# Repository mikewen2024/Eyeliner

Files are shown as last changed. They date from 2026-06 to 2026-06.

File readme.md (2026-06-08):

# Eyeliner — Melty-Brain Combat Robot

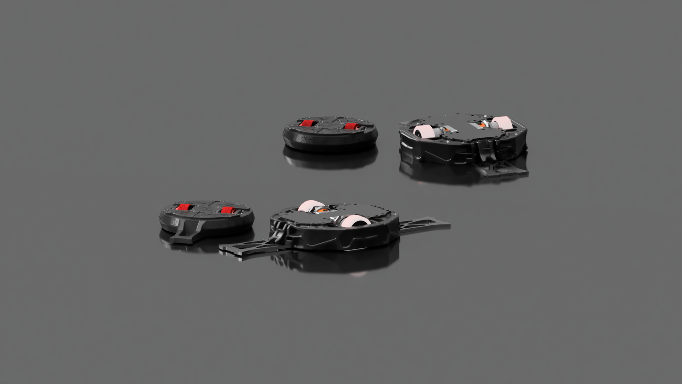
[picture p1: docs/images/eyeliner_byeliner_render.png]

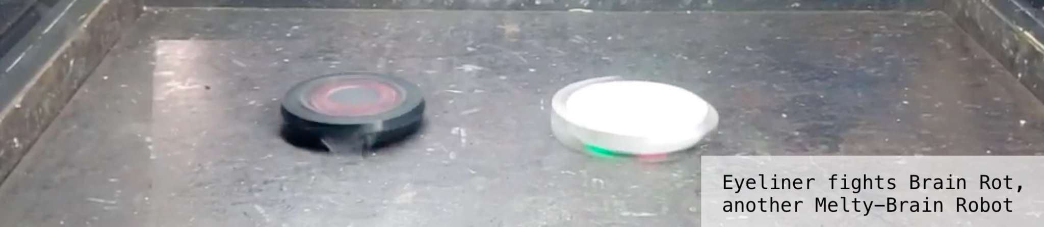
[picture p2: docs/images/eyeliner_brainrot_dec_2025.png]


A 1lb (antweight) melty-brain combat robot. A melty-brain spins the entire chassis at 1,000–2,000 RPM while pulsing drive motors ~100 times/second to achieve controlled translational movement — maximum hitting power, and one of the hardest archetypes to execute correctly.

**Key system requirements:** MHz-range onboard MCU, high-range accelerometer (~400g) for RPM/heading, per-motor drive current of ~30A (≈500W), and all electronics surviving constant 200–300g with peak impact accelerations orders of magnitude higher.

To read more about the development of the project and past versions, check out my personal technical blog [here](https://future-wool-0d5.notion.site/Eyeliner-Melty-brain-Combat-Robot-2ede4d628bf380b29920f43a3518d5c0) :)

---

## Current Iteration

**Hardware:** XIAO ESP32-S3 PLUS MCU, LSM6DSV320X IMU, Repeat Robotics BEC, ELRS nano receiver, dual 35A ESCs, ws2812b LED strip, Standalone ADXL-375 Accelerometer

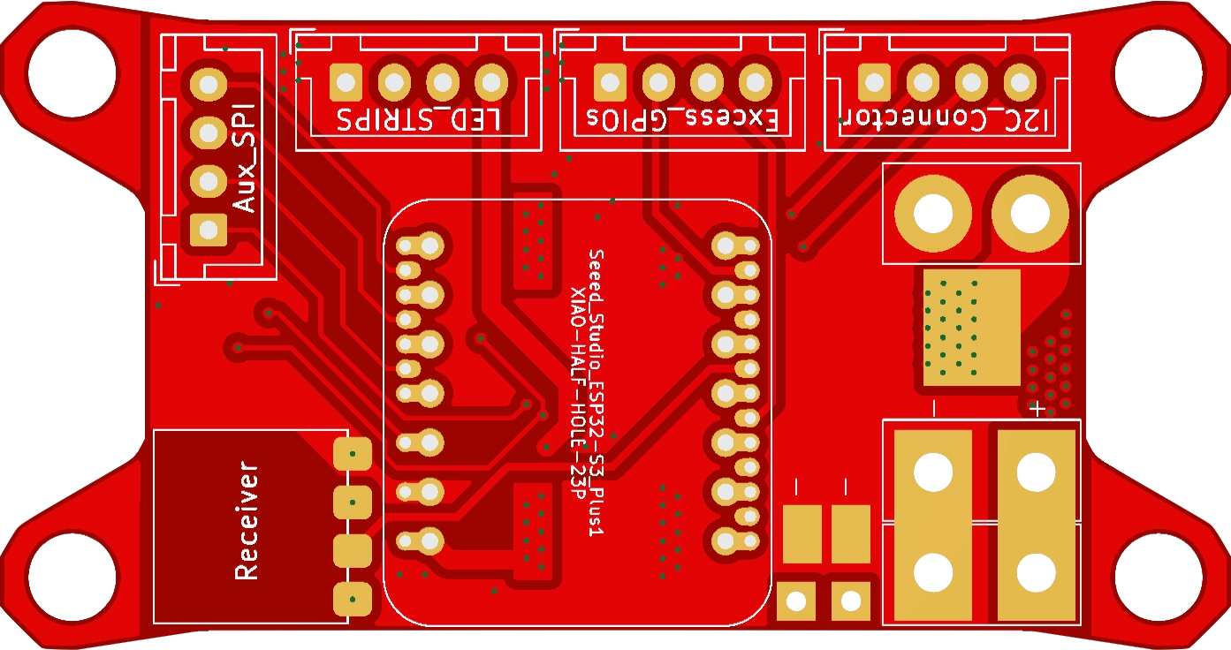
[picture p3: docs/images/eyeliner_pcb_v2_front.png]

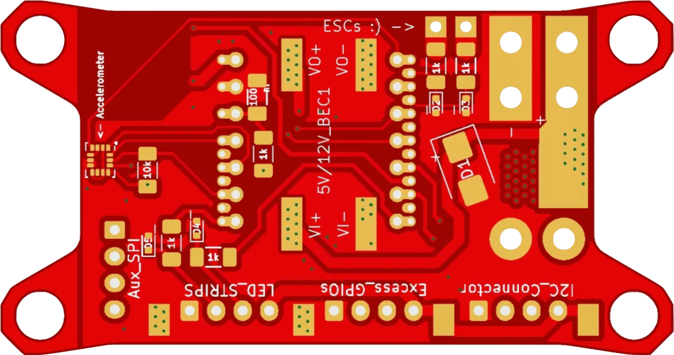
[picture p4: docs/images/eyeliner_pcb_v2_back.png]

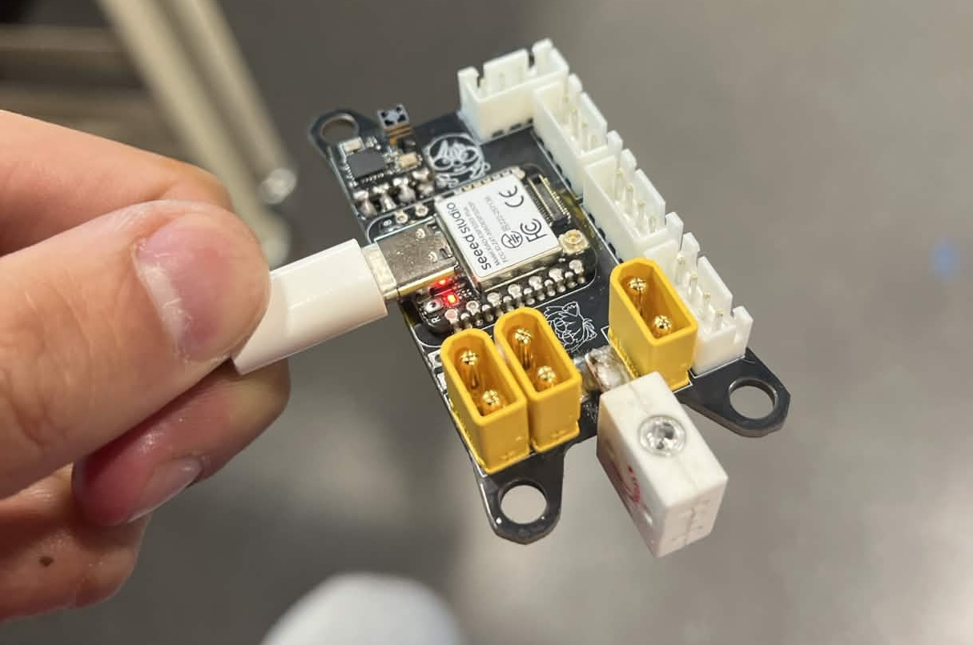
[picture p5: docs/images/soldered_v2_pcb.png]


**Key Features:**

- Extensive consideration for signal integrity, decoupling and bulk capacitance, and transients protection on all vulnerable MCU GPIO ports
- Made to run on 4s-6s LiHV with minimal changes (TVS diode change), interface with a range of possible sensors, and run interchangeably with antweight and beetleweight electronics
- Interchangeable high-kv 2207 "pacer" motors (outright top-range hitting power) and low-kv 2822 motors (faster spin-up with less current draw)
- LSM6DSV320X IMU with high and low range readout registers, built-in impact detection and interrupt capability, SPI interface 
- Custom UART interface for ELRS receiver to improve signal stability and expand channel bandwidth to 16 channels 
- LED strips for better heading and state indication
- Spare set of SPI connections for standalone ADXL375 or other sensors
- Shock isolated mounting with bracing for connectors
- Judicious ground plane placement for good return paths and receiver signal integrity, high-speed trace routing to reduce cross-talk and RC-loss, balancing current surge protection and voltage surge protection with TVS Diodes
- Up to 2500W burst capacity on HV side via solder busses, structural stability via extensive via stitching
- Spare GPIO connections for thermistors, IR sensors, etc...
- DSHOT600 and DSHOT1200 for high rate and accurate motor torque control at speed, built-in twisted-pairs for signal lines with GND return paths as close as possible to ESC grounds

**Upcoming Changes:** 

- Dual H3LIS331DL accelerometers (rotational speed without knowing center of rotation), easier-to-solder footprint
- More robust LDO system for 5V side
- Precharge circuit for higher-voltage inputs
- Two-way DSHOT for traction control
- Easily-removable high-speed connectors for ESCs
- Switch to STM32 for higher clock speeds, ESP32 for telemetry and LED control only
- Custom sensored ESCs
- Custom BMS

---

### Byeliner — Beetleweight Upscale V0 *(March 2026 – Present)*
**Class:** 3lb (beetleweight)
**Hardware Changes:** Oversize 790 kV 3548 motors, dual 80A 8s-capable VORTEX F65 ESCs, dual 4s LiHV batteries

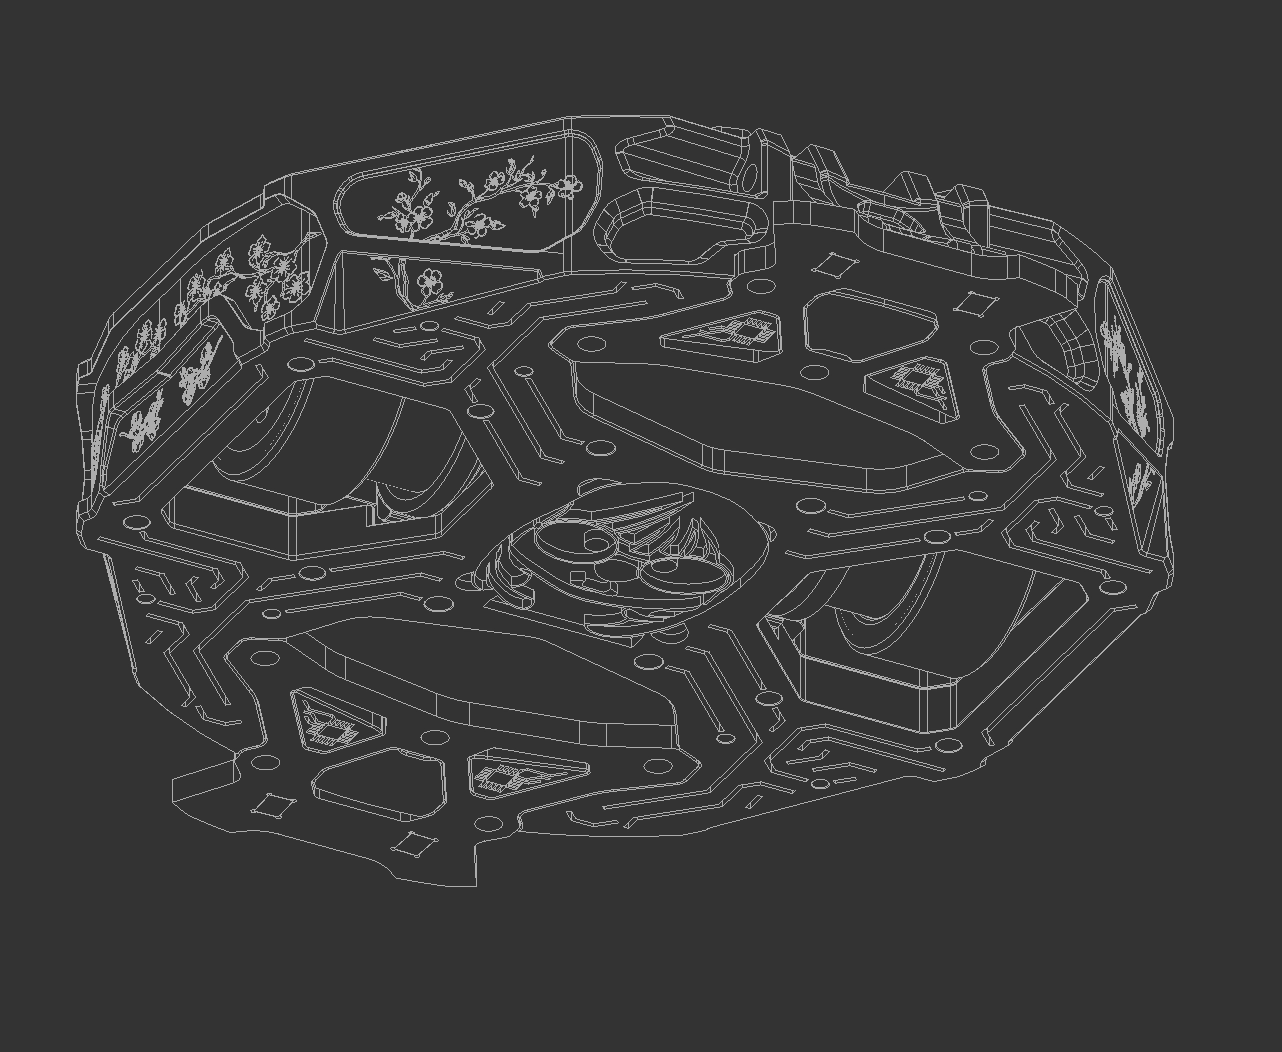
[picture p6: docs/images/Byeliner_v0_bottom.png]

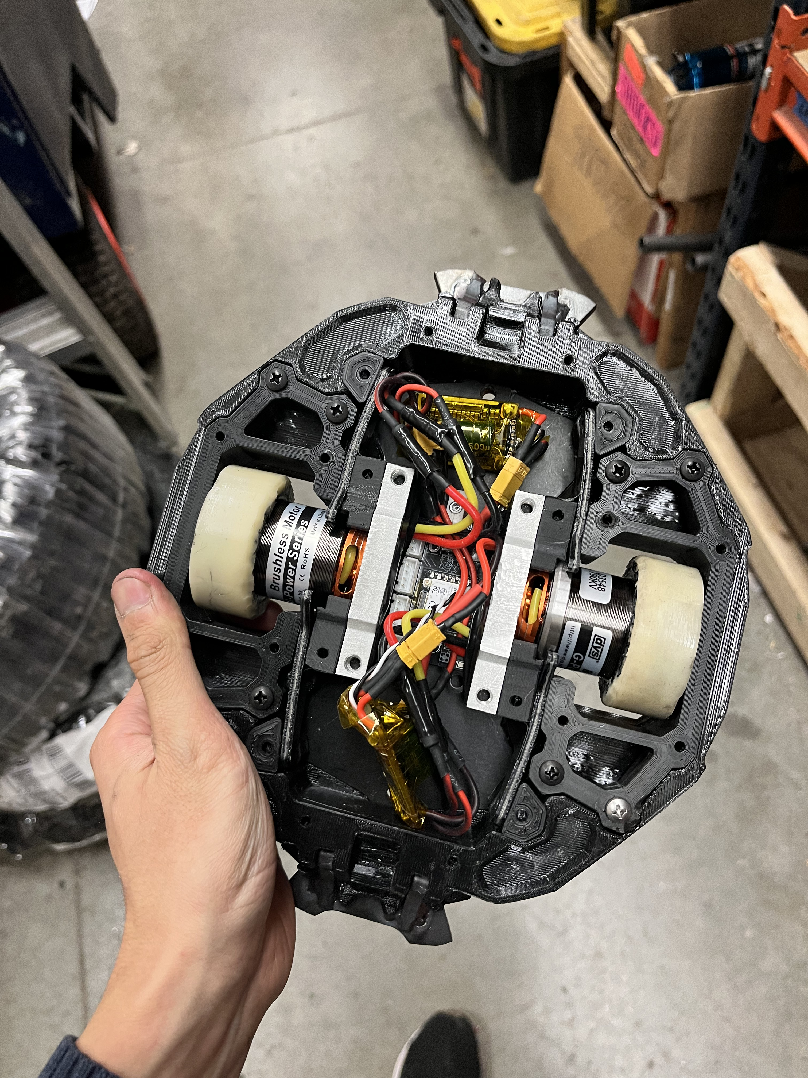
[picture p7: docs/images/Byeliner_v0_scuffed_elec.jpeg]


A 3lb version ("Byeliner") built for **Robobrawl**, early April 2026. The chassis is a rigid CURV and aluminum skeleton wrapped in TPU. On the code side, we are also moving towards platformIO for more organized operation.

---

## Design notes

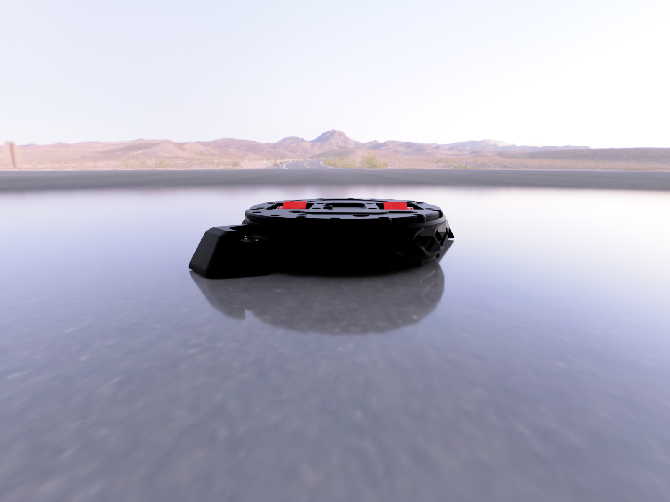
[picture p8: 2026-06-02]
docs/images/eyeliner_summer_2025_render.png

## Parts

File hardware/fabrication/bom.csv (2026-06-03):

Designator | Footprint | Quantity | Value | LCSC Part #
+, XT-30_VERT1, XT-30_VERT3 | XT-30_VERT | 3 | ~
100 | 1206 | 1 | 100 nF
10K, 1K | 1206 | 2 | 10k
1K_5, 1K_4, 1K_3, 1K_2 | 1206 | 4 | 1k
5V/12V_BEC1 | BEC_5V_12V | 1 | ~
<- ACCELEROMETER | LGA-14_3x2.5mm_P0.5mm_LayoutBorder3x4y | 1 | LSM6DSV320XTR
D1 | D_SMB | 1 | D_TVS
D2, D3 | D_SOD-523 | 2 | D_TVS
D4 | D_SOD-523 | 1 | D_LED_1
D5 | D_SOD-523 | 1 | D_LED_2
ESC1, ESC2 | ESC-PWM-Connection | 2 | ~
FINGERTECH_SWITCH1 | Fingertech_Switch | 1 | ~
J1 | JST_XH_B4B-XH-A_1x04_P2.50mm_Vertical | 1 | LED_STRIPS
J2 | JST_XH_B4B-XH-A_1x04_P2.50mm_Vertical | 1 | Aux_SPI
J3 | JST_XH_B4B-XH-A_1x04_P2.50mm_Vertical | 1 | I2C_Connector
J4 | JST_XH_B4B-XH-A_1x04_P2.50mm_Vertical | 1 | Excess_GPIOs
RECEIVER | BetaFPV ELRS Lite | 1 | ~
SEEED_STUDIO_ESP32-S3_PLUS1 | MOUDLE23P-SMD-2.54-21X17.8MM.kicad_mod.kicad_sym | 1 | XIAO-HALF-HOLE-23P
U1, U2, U3, U4, U5, U6 | Generic_SMD_THT | 6 | ~

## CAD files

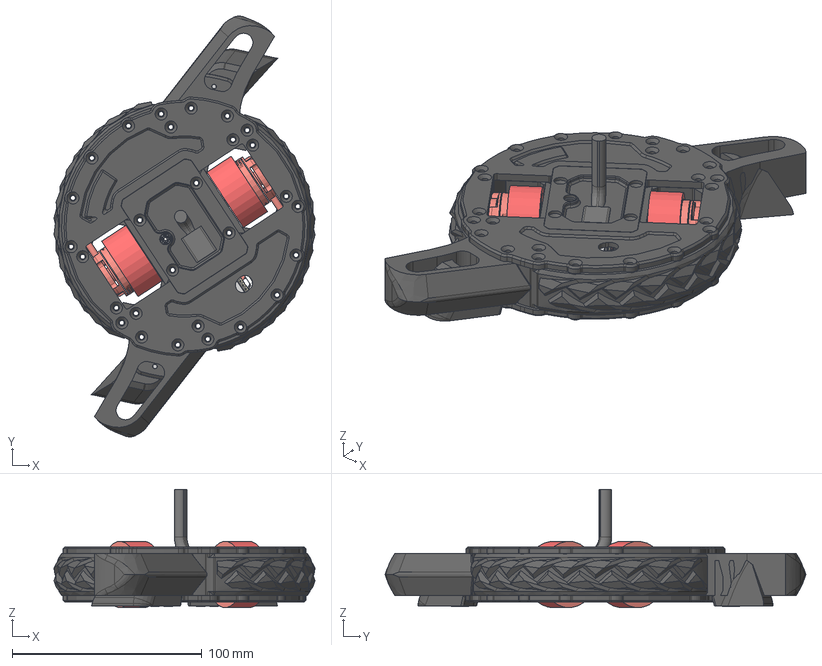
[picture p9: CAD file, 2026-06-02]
mechanical/PLANT_standalone_teeth/Main CAD.step
137.7 x 222.0 x 62.3 mm
Standard Weapon Teeth
BOSS-EXTRUDE14_8_
BOSS-EXTRUDE7_4_
BOSS-EXTRUDE7_3_
BOSS-EXTRUDE14_4_
BOSS-EXTRUDE14_2_
BOSS-EXTRUDE14_11_
BOSS-EXTRUDE7_7_
BOSS-EXTRUDE14_9_
BOSS-EXTRUDE14_3_
BOSS-EXTRUDE14_7_
MIRROR2
BOSS-EXTRUDE14_5_
BOSS-EXTRUDE14_12_
BOSS-EXTRUDE7_8_
BOSS-EXTRUDE7_1_
BOSS-EXTRUDE14_10_
BOSS-EXTRUDE7_9_
BOSS-EXTRUDE14_6_
BOSS-EXTRUDE14_1_
BOSS-EXTRUDE7_6_
BOSS-EXTRUDE7_2_
CUT-EXTRUDE5
BOSS-EXTRUDE7_5_
Shield
Pins x 2
U.FL-R-SMT-1_10_ v1
Placa_Base
PART A x 2
socket head cap screw_ai_HX-SHCS 0.086-56x0.375x0.375-S
TERMINAL x 2
The BEC
readytosky 35A esc x 2
Heat Sink
_autosave-Adafruit ADXL375_PCB
TYPE C TO RJ45
Receptor FS2A mini
Legs
PlasticHousing
5V GND
5V VCC
Receiver PWM Channels
I2C Lines
ESC PWM Lines
12V GND
12V VCC
Central Top Plate
Bottom Plate
Outer Top Plate
Chassis
7804K136_Stainless Steel Ball Bearing x 2
Motor x 2
ISO 4762 - M3 x 8 Steel 4.6 Plain x 8
90593A004_Black-Oxide Steel Hex Nut x 2
CRFCHTSTCTI ANSI B18.6.4 - 4-40 UNC x 0.75 Steel Grade 2 Plain x 6
Mesh Modifier x 2

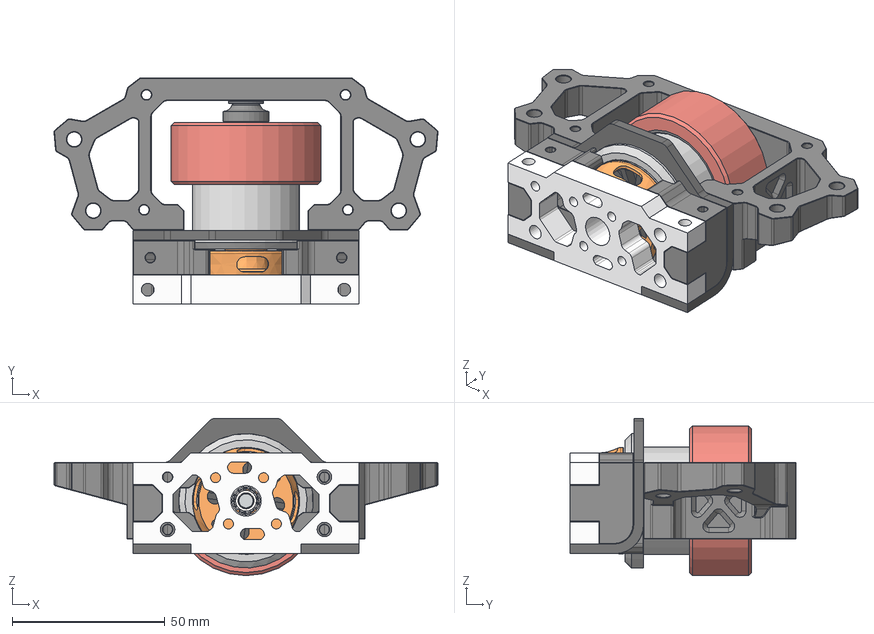
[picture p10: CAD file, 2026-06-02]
mechanical/Byeliner/Subcomponents/Wheel Stack.step
125.7 x 74.2 x 51.5 mm
D3548 - Moteur Brushless
Wheel
Mounting Block
Bearing
7804K136_Stainless Steel Ball Bearing
Tegris Support
Nylon Parts

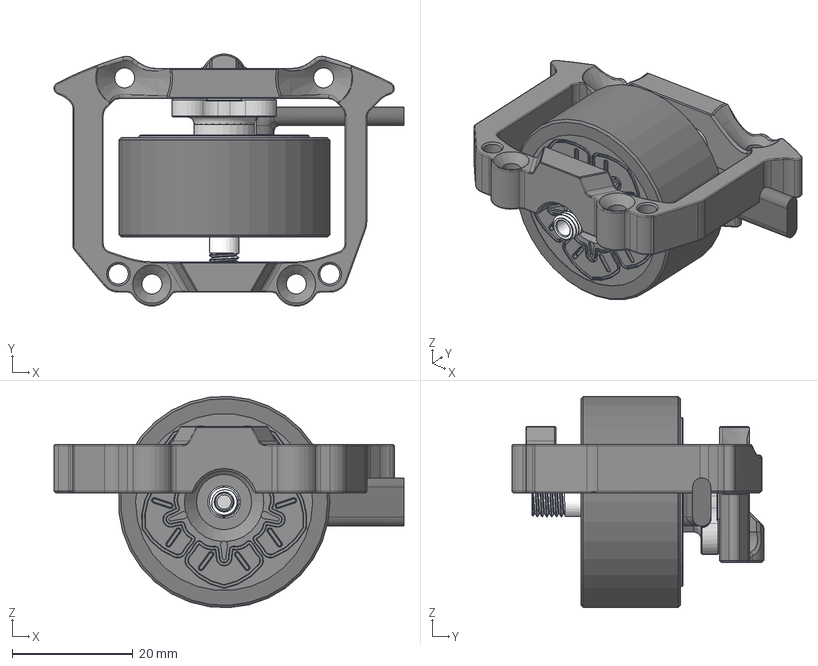
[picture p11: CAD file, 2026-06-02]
mechanical/PLANT_ring_chassis/Subcomponents/Pacer Motor Wheels.step
57.9 x 41.7 x 35.0 mm
Wheel Well Reference
ISO 7380-1 - M3 x 6 Steel 4.6 Plain
Wire Reference
Magnets
Coils
Base and Bearings
Wheel

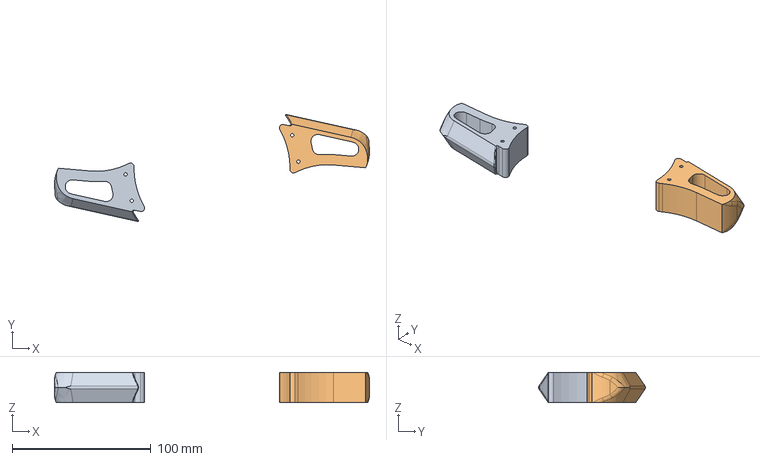
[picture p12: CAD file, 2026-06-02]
mechanical/PLANT_standalone_teeth/Subcomponents/Standard Weapon Teeth.step
227.4 x 77.3 x 22.0 mm

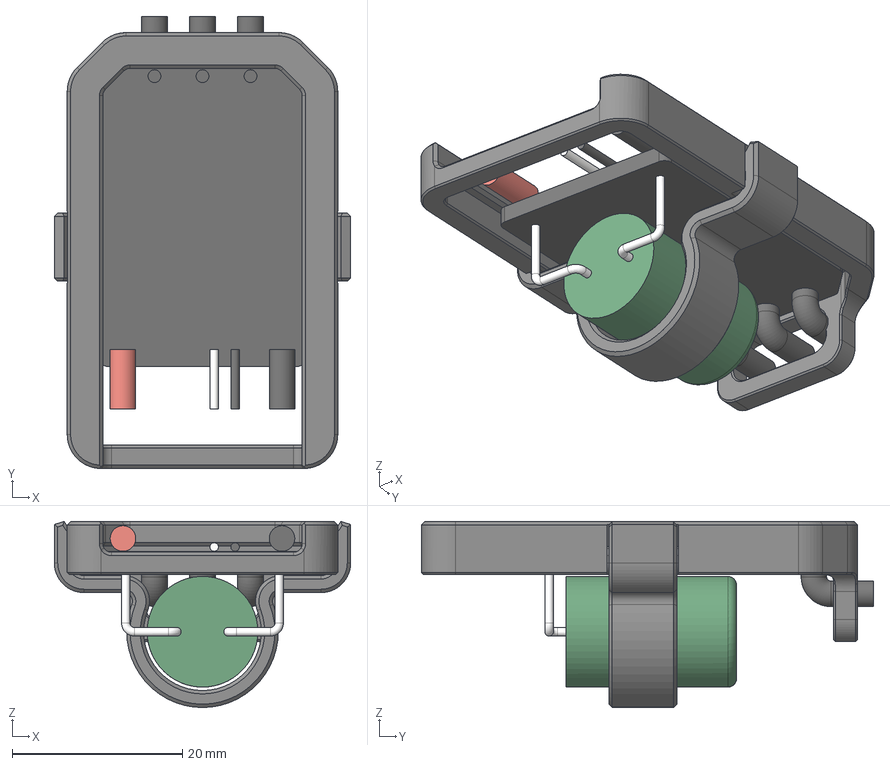
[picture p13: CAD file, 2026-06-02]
mechanical/Byeliner/Subcomponents/Vortex F65 ESC Harness.step
34.8 x 53.1 x 21.9 mm
Vortex 80A ESC stack
Harness

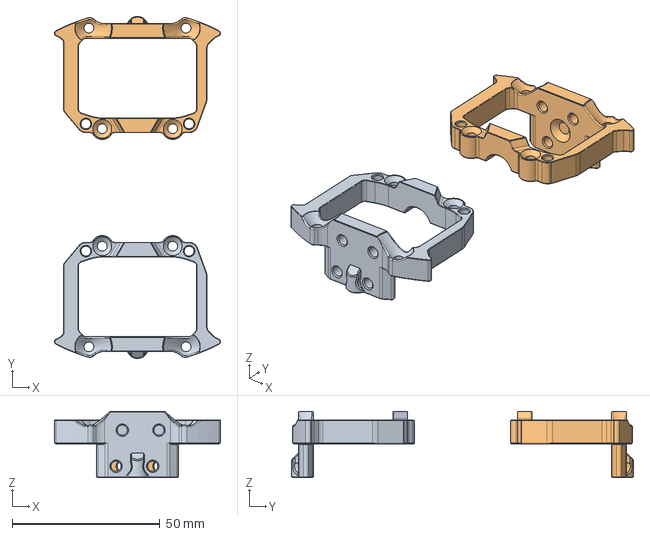
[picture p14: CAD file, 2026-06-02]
mechanical/PLANT_ring_chassis/Subcomponents/Wheel Wells for D2822 and Pacers.step
56.3 x 115.9 x 22.5 mm

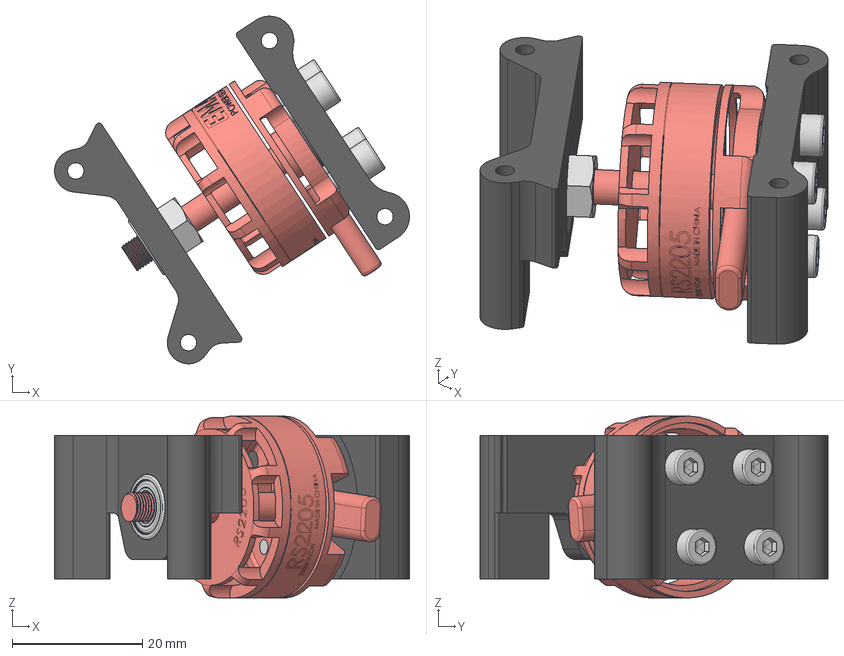
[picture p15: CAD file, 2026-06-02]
mechanical/PLANT_standalone_teeth/Subcomponents/Wheel Pod.step
54.4 x 53.3 x 27.9 mm
7804K136_Stainless Steel Ball Bearing
Motor
ISO 4762 - M3 x 8 Steel 4.6 Plain x 4
90593A004_Black-Oxide Steel Hex Nut

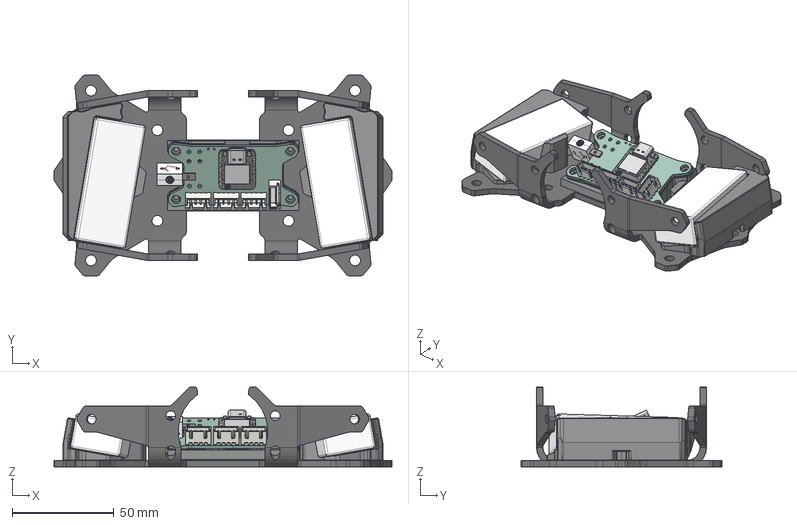
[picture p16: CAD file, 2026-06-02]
mechanical/Byeliner/Subcomponents/Elec Housings.step
165.8 x 98.6 x 39.1 mm
Elec Holder
JST_B4B_XH_A x 4
R_1206_3216Metric_6 x 6
D_SOD_523 x 4
D_SMB_1
LGA_14_3x25mm_P05mm_LayoutBorder3x4y
C_1206_3216Metric_1
Eyeliner-PCB-V2_PCB
PART A x 2
socket head cap screw_ai_HX-SHCS 0.086-56x0.375x0.375-S
TERMINAL x 2
BOSS-EXTRUDE14_8_
BOSS-EXTRUDE7_4_
BOSS-EXTRUDE7_3_
BOSS-EXTRUDE14_4_
BOSS-EXTRUDE14_2_
BOSS-EXTRUDE14_11_
BOSS-EXTRUDE7_7_
BOSS-EXTRUDE14_9_
BOSS-EXTRUDE14_3_
BOSS-EXTRUDE14_7_
MIRROR2
BOSS-EXTRUDE14_5_
BOSS-EXTRUDE14_12_
BOSS-EXTRUDE7_8_
BOSS-EXTRUDE7_1_
BOSS-EXTRUDE14_10_
BOSS-EXTRUDE7_9_
BOSS-EXTRUDE14_6_
BOSS-EXTRUDE14_1_
BOSS-EXTRUDE7_6_
BOSS-EXTRUDE7_2_
CUT-EXTRUDE5
BOSS-EXTRUDE7_5_
Shield
Pins x 2
U.FL-R-SMT-1_10_ v1

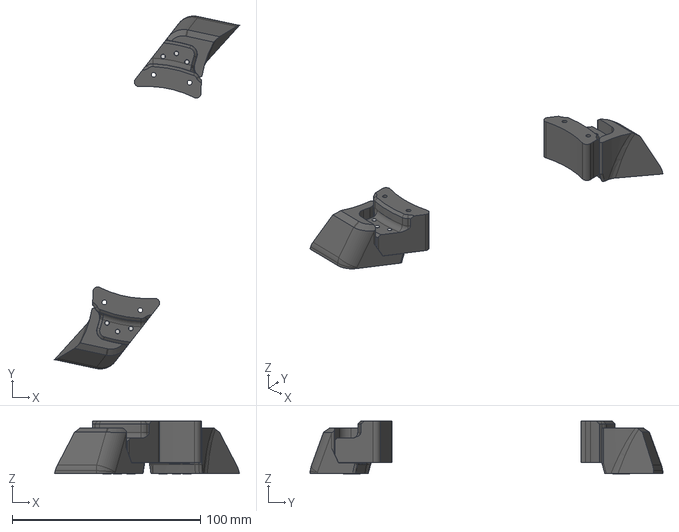
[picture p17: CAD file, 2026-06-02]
mechanical/PLANT_standalone_teeth/Subcomponents/Undercutter Config.step
98.2 x 187.3 x 27.9 mm
CRFCHTSTCTI ANSI B18.6.4 - 4-40 UNC x 0.75 Steel Grade 2 Plain x 6

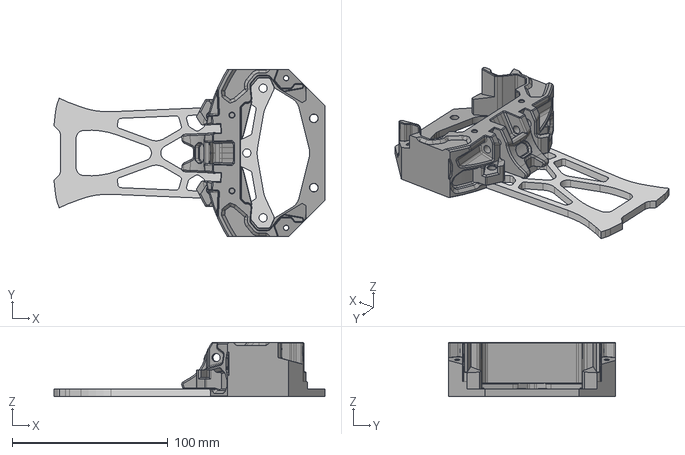
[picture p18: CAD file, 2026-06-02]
mechanical/Byeliner/Subcomponents/Reach Tooth (5mm AR600 version) v6.step
174.2 x 107.6 x 34.9 mm
Reference Mounting Geometry
Reach Tooth

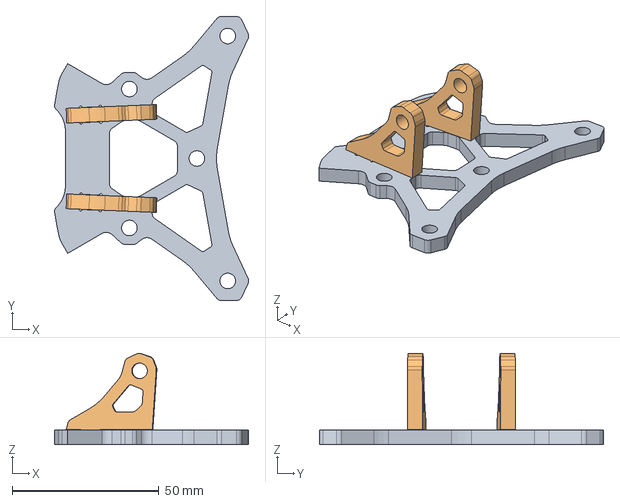
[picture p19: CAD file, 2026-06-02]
mechanical/Byeliner/Subcomponents/Basic Teeth.step
66.1 x 96.6 x 31.0 mm

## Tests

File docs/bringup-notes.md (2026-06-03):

# Bring-Up Notes: Eyeliner
**Lead Engineer:** Mike Wen

---

## Latest Iterations

### Byeliner — Beetleweight Upscale V0 *(March 2026 – Present)*
**Class:** 3lb (beetleweight)
**Hardware Changes:** Oversize 790 kV 3548 motors, dual 80A 8s-capable VORTEX F65 ESCs, dual 4s LiHV batteries

Graph Graphic
Graph Graphic

A 3lb version ("Byeliner") built for **Robobrawl**, early April 2026. The chassis is a rigid CURV and aluminum skeleton wrapped in TPU. On the code side, we are also moving towards platformIO for more organized operation.

---

### V2 PCB — Second Electronics Revision *(January – March 2026)*
**Hardware:** XIAO ESP32-S3 PLUS MCU, LSM6DSV320X IMU, Repeat Robotics BEC, ELRS nano receiver, dual 35A ESCs, ws2812b LED strip, Standalone ADXL-375 Accelerometer, redesigned compact PCB

Graph Graphic
Graph Graphic
Graph Graphic

More cautious design process — reviewed by ~6 upperclassmen and EE professionals, with stringent checks for signal integrity, DFM, intercction between interfaces with each component, and transients protection at each level. Much more compact layout than V1. The LGA package high range accelerometer worked first try despite having 12 closely-spaced (0.1mm spacing) pins blindly soldered on the bottom of the package.

- Changed to "PLUS" layout of MCU for more GPIO ports
- Extensive consideration for signal integrity, decoupling and bulk capacitance, and transients protection on all vulnerable MCU GPIO ports
- Made to run on 4s-6s LiHV with minimal changes (TVS diode change), interface with a range of possible sensors, and run interchangeably with antweight and beetleweight electronics
- Interchangeable high-kv 2207 "pacer" motors (outright top-range hitting power) and low-kv 2822 motors (faster spin-up with less current draw)
- LSM6DSV320X IMU with high and low range readout registers, built-in impact detection and interrupt capability, SPI interface 
- Custom UART interface for ELRS receiver to improve signal stability and expand channel bandwidth to 16 channels 
- LED strips for better heading and state indication
- Spare set of SPI connections for standalone ADXL375 or other sensors
- Shock isolated mounting with bracing for connectors
- Judicious ground plane placement for good return paths and receiver signal integrity, high-speed trace routing to reduce cross-talk and RC-loss, balancing current surge protection and voltage surge protection with 
- Up to 2500W burst capacity on HV side via solder busses, structural stability via extensive via stitching
- Spare GPIO connections for thermistors, IR sensors, etc...
- Switched to DSHOT600 and DSHOT1200 for better motor control, built-in twisted-pairs for signal lines with GND return paths as close as possible to ESC grounds
- Kept BEC off-the-shelf since I had a lot of spares on hand and wanted to save costs

Remaining issues on first board: BEC footprint was flipped again (oops!), BEC needs to be swapped out eventually for smaller footprint and more stable 5V output, slight voltage surge on 5V side would fry all downstream 5V-to-VDDIO regulators

---

### V1.5 — Organizational Lessons *(June – December 2025)*

**Hardware:** XIAO ESP32-S3 MCU, Repeat Robotics BEC, dual 32-bit 35A ESCs, 4-channel FS2A  Receiver, Standalone ADXL-375 Accelerometer

Focused on identifying layout and harness mistakes from the first two-thirds of the year: radially-routed wires stressed solder joints, ESCs sat directly under the battery, and shock isolation was inadequate. Groundwork laid for a proper second PCB attempt.

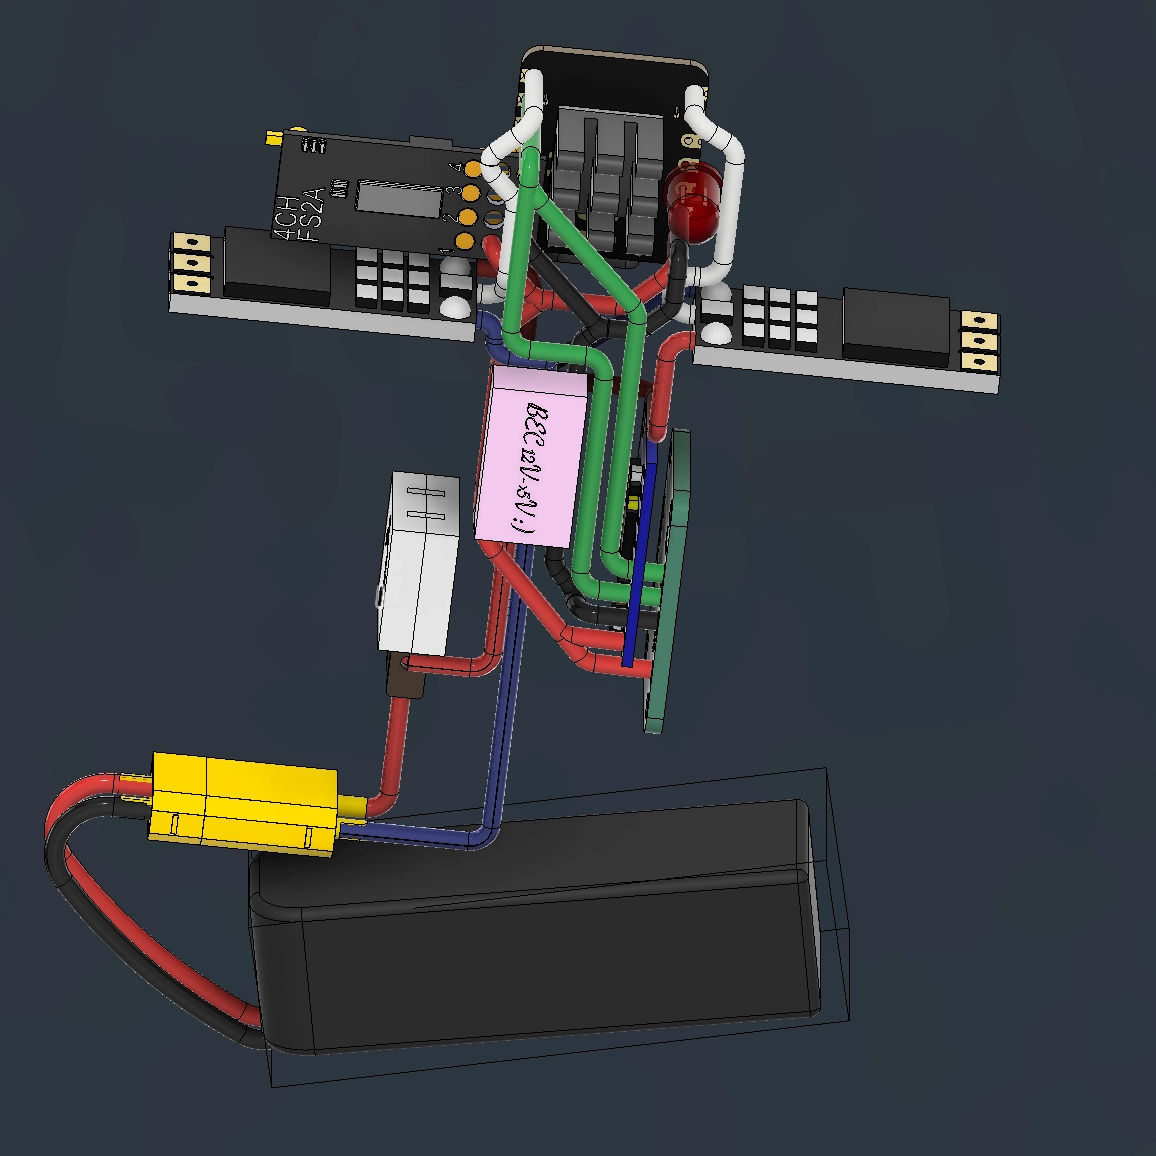
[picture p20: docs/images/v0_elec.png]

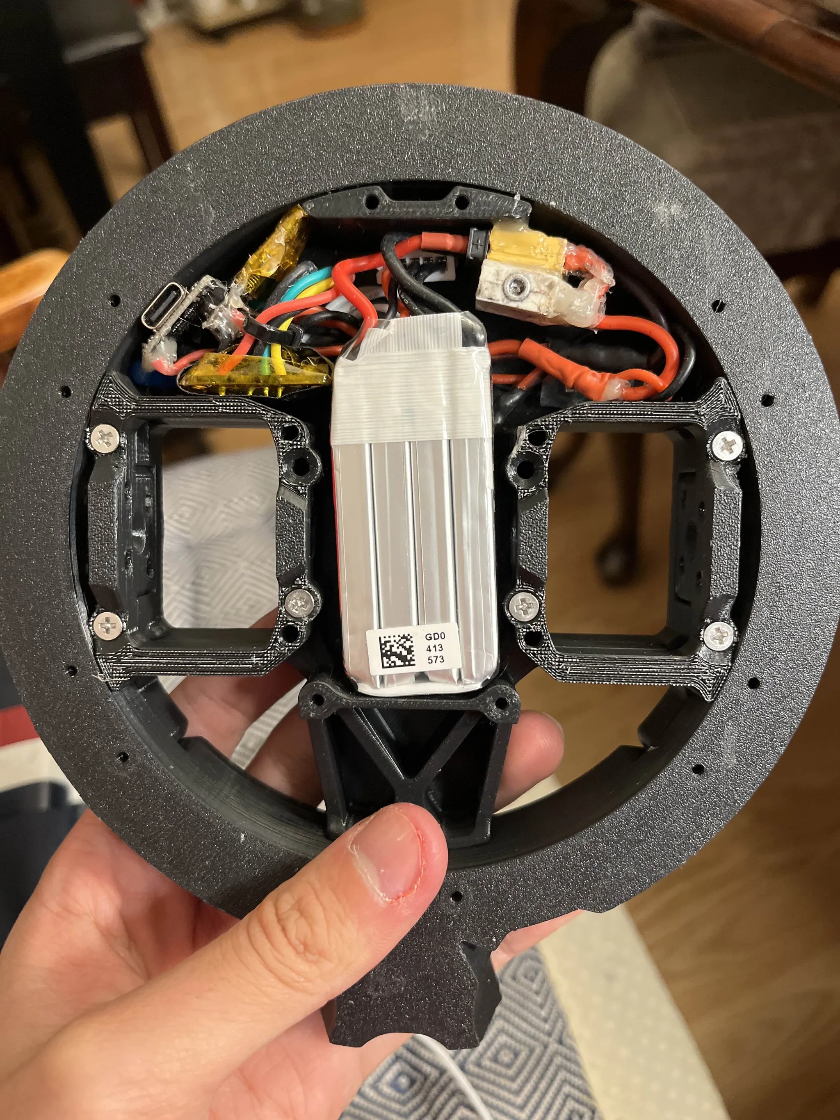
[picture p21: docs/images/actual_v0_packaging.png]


Over two competitions during summer 2025 and a few in the fall, I learned a lot about how to secure electronics in high impact environments and probably took a few too many pitfalls in putting off a second version of the PCB. The bot could consistently maintain heading throughout the RPM range and exhibit some translational control while spun-up, and could slug it out over a full day of successive 3-minute matches. However, reliability on the logic side was still lacking, with the power output and inefficiency of the cheap high-kV 2205 motors being the main limiting factor for spin-up performance.

- Structural changes to reduce stress risers
- Improved part replaceability and modularity
- Wheels and impactors now swappable
- Chassis is still compatible with newer electricals
- Moved to higher discharge capability 3s LiHV battery

Key issues: Delicate 22 gauge wire connections on logic side (despite strain leaving wire length in the harness for strain relief) tended to pull out under impact. Solder joints were prone to fatigue over many testing and match cycles, wires sometimes failed far from solder joints. Digital interrupt-based "clock recovery" often resulted in bad PWM signal integrity from receiver.

---

### V1 PCB — First Electronics Revision *(February 2025)*
**Hardware:** Seeed Studio XIAO ESP32-MG24 SENSE MCU, 4-channel FS2A  Receiver, dual 32-bit 35A ESCs, custom PCB (first attempt)

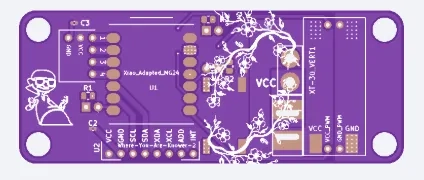
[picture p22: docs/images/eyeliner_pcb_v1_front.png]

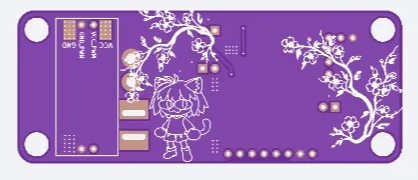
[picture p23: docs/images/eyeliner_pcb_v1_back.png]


First PCB design attempt. Notable mistakes:
- BEC footprint flipped — had to solder the module on backwards
- All SMD component footprints were one size too large, requiring sketchy diagonal mounting
- Power switch placed in an inaccessible orientation
- ESP32-MG24 SENSE line proved wholly unsuited to high-fidelity PWM output
- Decoupling caps downstream of BEC caused every board to short 5V to GND
- Initially used MPU6050 footprint before defaulting to high-range accelerometer
- Repeat "AM32 Drive ESCs" - 32-bit firmware running on custom settings for torque
- Lower discharge 3s LiPo battery

Iterated MCU choices through ESP32-WROOM → XIAO S3, which proved reliable. PCB effectively non-functional; bot continued to run on discrete wiring.

---

### V0 — Initial Development *(August 2024 – May 2025)*
**Hardware:** 2× RS2205 motors, BLHeli_S ESCs (8-bit), Teensy 4.1, MPU6050 IMU, 4-channel FS2A  Receiver

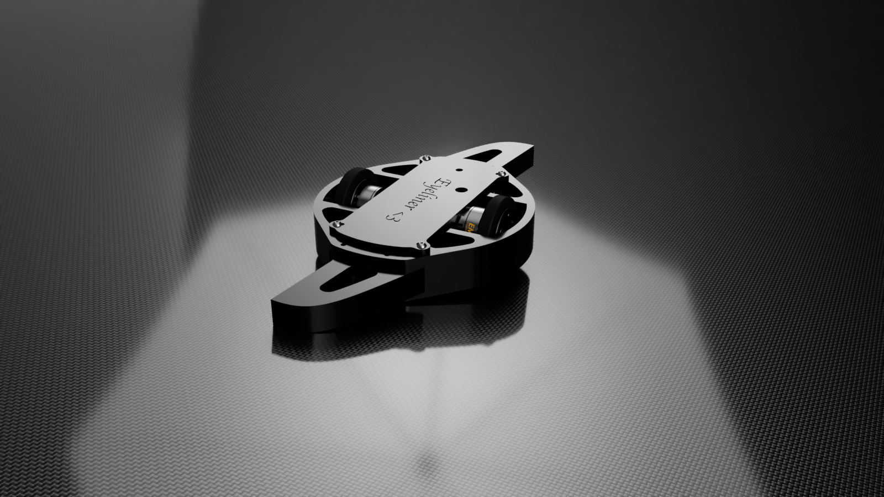
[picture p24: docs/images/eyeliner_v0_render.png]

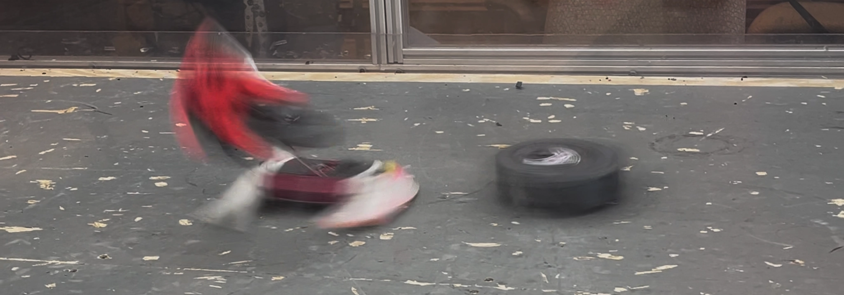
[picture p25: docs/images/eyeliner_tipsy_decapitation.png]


First build; no PCB, hand-wired harness. Major issues included:
- MPU6050 maxes out at ~600 RPM — inadequate for a melty-brain
- BLHeli_S ESC arming/failsafe behavior was poorly documented and unreliable
- Teensy 4.1 burned out from a poor soldering job
- Eventual switch to Seeed Studio XIAO ESP32-S3 for compactness
- Switch to ADXL375 breakout board for high-range accelerometer

Competed December 2024 in "dumb melty" mode (receiver wired directly to ESCs). Still landed solid hits, including splitting an opponent's chassis. Informal May 2025 comp ran the same way — destroyed several opponents' weapons.

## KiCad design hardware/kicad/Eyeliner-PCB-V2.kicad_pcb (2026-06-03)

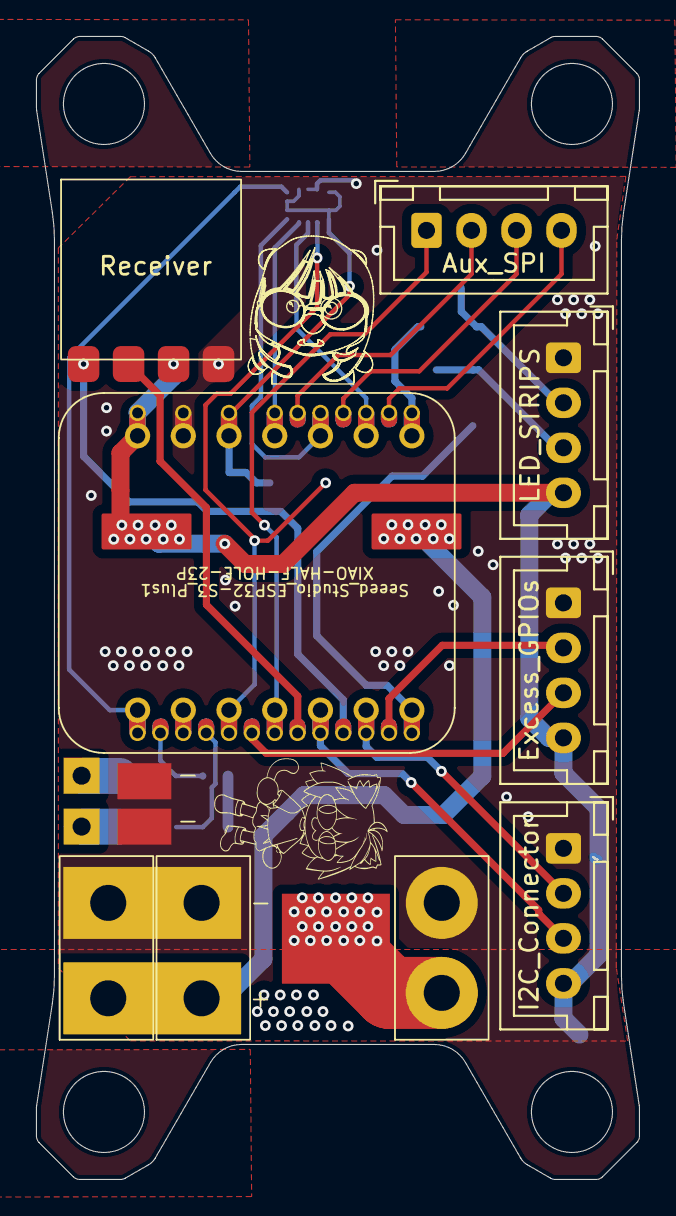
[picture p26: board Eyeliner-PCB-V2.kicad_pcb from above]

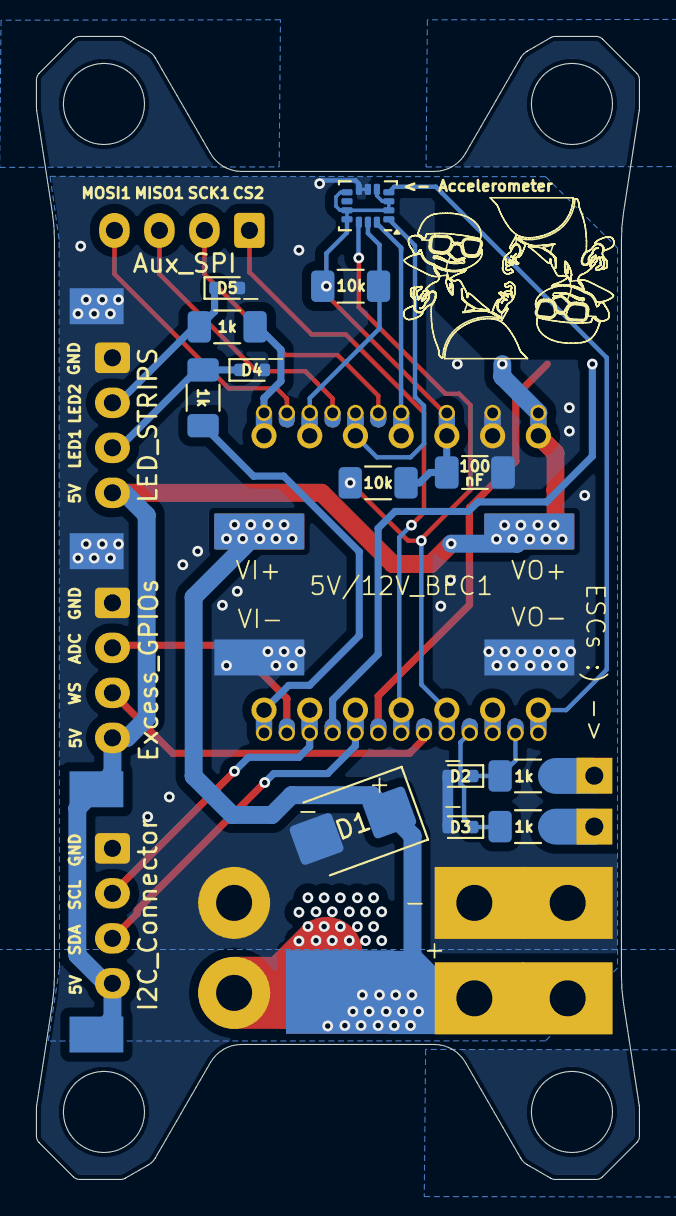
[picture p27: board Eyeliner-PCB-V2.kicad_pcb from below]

Board: 2 copper layers, 33.5 x 63.5 mm, 32 parts (17 on the bottom side), 28 nets.

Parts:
1k, 1k#2, 1k#3, 1k#4: 1k; R_1206_3216Metric_Pad1.30x1.75mm_HandSolder
5V/12V_BEC1: BEC_5V_12V
10k, 10k#2: 10k; R_1206_3216Metric_Pad1.30x1.75mm_HandSolder
100: 100 nF; C_1206_3216Metric_Pad1.33x1.80mm_HandSolder
+: XT-30_VERT
<- Accelerometer: LSM6DSV320XTR; LGA-14_3x2.5mm_P0.5mm_LayoutBorder3x4y
D1: D_TVS; D_SMB
D2, D3: D_TVS; D_SOD-523
D4: D_LED_1; D_SOD-523
D5: D_LED_2; D_SOD-523
ESC1, ESC2: ESC-PWM-Connection
Fingertech_Switch1: Fingertech_Switch
J1: LED_STRIPS; JST_XH_B4B-XH-A_1x04_P2.50mm_Vertical
J2: Aux_SPI; JST_XH_B4B-XH-A_1x04_P2.50mm_Vertical
J3: I2C_Connector; JST_XH_B4B-XH-A_1x04_P2.50mm_Vertical
J4: Excess_GPIOs; JST_XH_B4B-XH-A_1x04_P2.50mm_Vertical
Receiver: BetaFPV ELRS Lite
Seeed_Studio_ESP32-S3_Plus1: XIAO-HALF-HOLE-23P; MOUDLE23P-SMD-2.54-21X17.8MM.kicad_mod.kicad_sym
U1, U2, U3, U4, U5, U6: Generic_SMD_THT
XT-30_VERT1, XT-30_VERT3: XT-30_VERT

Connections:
4S_VCC: 5V/12V_BEC1.VIN+, +.VCC, D1.1 (K), Fingertech_Switch1.OUT, XT-30_VERT1.VCC
ADC_BAT: J4.2, Seeed_Studio_ESP32-S3_Plus1.20 (GPIO10_XMCLK/ADC_BAT)
CS_1: 10k.2, <- Accelerometer.12 (CS), Seeed_Studio_ESP32-S3_Plus1.3 (GPIO3_D2/A2)
CS_2: J2.1, Seeed_Studio_ESP32-S3_Plus1.4 (GPIO4_D3/A3)
ESC_1: 1k#3.2, D2.1 (K), Seeed_Studio_ESP32-S3_Plus1.15 (GPIO38_DVP_VSYNC/I2S_SD)
ESC_2: 1k.2, D3.1 (K), Seeed_Studio_ESP32-S3_Plus1.16 (GPIO39_CAM_SCL/I2S_SCK)
GND: 5V/12V_BEC1.VIN-, 5V/12V_BEC1.VO-, 100.2, +.GND, <- Accelerometer.6 (GND), <- Accelerometer.7 (GND), D1.2 (A), D2.2 (A), D3.2 (A), D4.2 (A), D5.2 (A), J1.1, J3.1, J4.1, Receiver.4 (GND), Seeed_Studio_ESP32-S3_Plus1.13 (GND), U1.1 (GND), U2.1 (GND), U3.1 (GND), U5.1 (GND), XT-30_VERT1.GND, XT-30_VERT3.GND
INT_1: <- Accelerometer.4 (INT1), Seeed_Studio_ESP32-S3_Plus1.1 (GPIO1_D0/A0)
LED_1: 1k#4.2, Seeed_Studio_ESP32-S3_Plus1.7 (U0TXD_D6/TX)
LED_2: 1k#2.2, Seeed_Studio_ESP32-S3_Plus1.8 (U0RXD_D7/RX)
MISO: <- Accelerometer.1 (SDO/TA0), Seeed_Studio_ESP32-S3_Plus1.10 (GPIO8_D9/A9/MISO)
MISO1: J2.3, Seeed_Studio_ESP32-S3_Plus1.22 (GPIO12_DVP_Y7/SPI_MISO1)
MOSI: <- Accelerometer.14 (SDA), Seeed_Studio_ESP32-S3_Plus1.11 (GPIO9_D10/A10/MOSI)
MOSI1: J2.4, Seeed_Studio_ESP32-S3_Plus1.21 (GPIO11_DVP_Y8/SPI_MOSI1)
unnamed: 1k#4.1, D4.1 (K), J1.3
unnamed: 1k#2.1, D5.1 (K), J1.2
unnamed: 1k#3.1, ESC1.1 (PWM)
unnamed: 1k.1, ESC2.1 (PWM)
Receiver_RX: Receiver.1 (RX), Seeed_Studio_ESP32-S3_Plus1.19 (GPIO42_PDM_CLK/TX1)
Receiver_TX: Receiver.2 (TX), Seeed_Studio_ESP32-S3_Plus1.18 (GPIO41_PDM_DATA/RX1)
SCK: 10k#2.2, <- Accelerometer.13 (SCL), Seeed_Studio_ESP32-S3_Plus1.9 (GPIO7_D8/A8/SCK)
SCK1: J2.2, Seeed_Studio_ESP32-S3_Plus1.23 (GPIO13_DVP_PCLK/SPI_SCK1)
SCL: J3.2, Seeed_Studio_ESP32-S3_Plus1.6 (GPIO6_D5/A5/I2C_SCL)
SDA: J3.3, Seeed_Studio_ESP32-S3_Plus1.5 (GPIO5_D4/A4/I2C_SDA)
SWITCH INPUT: Fingertech_Switch1.IN, XT-30_VERT3.VCC
VCC 3V3: 10k.1, 10k#2.1, 100.1, <- Accelerometer.2 (SDX), <- Accelerometer.3 (SCX), <- Accelerometer.5 (VDDIO), <- Accelerometer.8 (VDD), <- Accelerometer.10 (OCS_AUX), <- Accelerometer.11 (SDO_AUX), Seeed_Studio_ESP32-S3_Plus1.12 (VCC_3V3)
VCC 5V: 5V/12V_BEC1.VO+, J1.4, J3.4, J4.4, Receiver.3 (5V), Seeed_Studio_ESP32-S3_Plus1.14 (VBUS), U4.1 (VCC), U6.1 (VCC)
WS: J4.3, Seeed_Studio_ESP32-S3_Plus1.17 (GPIO40_CAM_SDA/I2S_WS)

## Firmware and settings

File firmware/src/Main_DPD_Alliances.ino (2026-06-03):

/* Libraries Used */
// ADXL library and sensor libraries used
#include <Wire.h>
#include <Adafruit_Sensor.h>
#include <Adafruit_ADXL375.h>

// LSM library and sensor libraries used
#include <Wire.h>
#include <SPI.h>

// Motor control -- DShot! 
#include <Arduino.h>
#include <DShotRMT.h>

// Motor control (currently not DShot, just PWM)
#include <ESP32Servo.h> 

#include <FastLED.h>

// For modf
#include <cmath>

/* Conditional Macros */
// #define DISPLAY_SERIAL // Runs serial outputs
#undef DISPLAY_SERIAL
// #define ESP_NOW // Runs ESP as transmitter for ESP-Now
#undef ESP_NOW
#define MOTORS // Enables motors
// #undef MOTORS

/* Forward Declarations */
// From FS2A_Receiver.ino
bool setupReceiver();
void updateTiming();
bool readChannels();
void remapInputs();

// From ADXL375_Heading.ino
bool setupHeading();
bool updateHeading(float COR_Input);
float updateHeadingDotProduct(float throttle_x, float throttle_y);
void indicateHeading();

// From Motor_Control.ino
// bool setupMotorsPWM();
bool setupMotorsDshot(); 
bool stopLogic(float throttle_spinup, float throttle_x, float throttle_y, float heading_cosine);
// void killMotorsPWM(); 
void killMotorsDshot(); 

// Tracks whether or not setup was successful
bool setupSuccessful = true;

/* Dynamic variables and objects from each file */
// From ADXL375_Heading.ino
/* In-code objects */
Adafruit_ADXL375 accel = Adafruit_ADXL375(12345);
sensors_event_t event;

/* Dynamically-Updated Variables */
// Accelerometer reading
unsigned long last_read = 0; // Last time accelerometer was read in
float raw_acceleration = 0.0f;
float processed_acceleration = 0.0f;

// COR
float radius_of_rotation = 0.0f; // Radius of rotation in millimeters
float last_radius_of_rotation = 0.0f;

// Outputs
float degrees_per_second = 0.0f; // Rotation rate
float previous_degrees_per_second = 0.0f; // Last measured rotation rate for 
float heading_degrees = 0.0f; // Should only be positive for now

// Auxillary variables for calculating dot product b/w heading and throttle
float heading_x = 0.0f;
float heading_y = 0.0f;
float throttle_magnitude = 0.0f;
float heading_translation_dot_product = 0.0f;

// From FS2A_Receiver.ino
// Channel-specific timing deltas
// Available denotes "available to be read-in"
volatile unsigned long channelBeginTimes[4];
volatile unsigned long channelEndTimes[4];
volatile bool channelAvailabilities[4];

// Raw channel data and last channel data information for low-pass
// Channel 1: Left X, left = 1000, right = 2000
// Channel 2: Left Y, down = 1000, up = 2000
// Channel 3: Right Y, down = 1000, up = 2000
// Channel 4: Right X, left = 1000, right = 2000
int rawChannelData[4]; 
int lastChannelData[4]; // No low-pass filter implemented for now, not needed
float remappedChannelData[4]; // [-1, 1] Range
int channelDefaults[4];

// General timing deltas
int current_micros = 0.0f;
int last_micros = 0.0f;
int delta_micros = 0.0f;
float ticks_per_second = 0.0f; // Only calculate if needed for telemetry
bool safe_to_read = false;

// From Motor_Control.ino
// This determines the threshold on the cosine b/w translation direction and heading to trigger braking
#define HEADING_THRESHOLD 0.96f

// Dynamically-updated variables
// Translational throttle magnitude, has a dead zone
float D = 0.0f;
float M = 0.0f;
float Modulation = 0.0f;
float Amplitude_Modulation = 0.0f;
float Motor_1_Throttle = 0.0f;
float Motor_2_Throttle = 0.0f;

// Setup :)
void setup() {
  #ifdef DISPLAY_SERIAL
    Serial.begin(115200); // Start serial communication
  #endif

  // Setup receiver channels

  // Uncomment for FS2A
  // if (!setupReceiver()) setupSuccessful = false;

  // Uncomment for ELRS
  setupELRSReceiver();

  #ifdef MOTORS
    // Motor setup -- choose setup! 
    // if (!setupMotorsPWM()) setupSuccessful = false;
    if (!setupMotorsDshot()) setupSuccessful = false;
  #endif

  // Accelerometer and heading indication setup

  // Uncomment for ADXL
  // if (!setupHeading()) setupSuccessful = false;

  // Uncomment for LSM
  if (!setupHeadingLSM()) setupSuccessful = false;

  #ifdef DISPLAY_SERIAL
      Serial.println("Setup Finished :)");
  #endif
}

void loop() {
    // Update timing and receiver inputs first
    updateTiming();
    // if (!readChannels()) {
    //   killMotors();
    //   return;
    // }
    if (!readChannelsELRS()) {
      killMotorsDshot();
      // killMotorsPWM(); 
      return;
    }
    remapInputs();

    // Handle accelerometer updates
    // updateHeading(remappedChannelData[1]);
    updateHeadingLSM(remappedChannelData[1]);
    updateHeadingDotProductLSM(remappedChannelData[3], remappedChannelData[2]);
    indicateHeadingLSM();
    
    // Motor control code
    stopLogic(remappedChannelData[0], remappedChannelData[3], remappedChannelData[2], heading_translation_dot_product);
}

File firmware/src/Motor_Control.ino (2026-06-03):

// Motor definition / declaration for PWM are done here, we only use them in this file
#define ESC_1 38
#define ESC_2 39

Servo esc1;
Servo esc2;

/* Constants used */

// // ESC settings - PWM
#define HIGH_SIGNAL 2000
#define LOW_SIGNAL 1000
#define NEUTRAL 1500

// ESC setting important variables
int MAX_THROTTLE_DEVIATION = 500.0f;

// ±10˚ off center, braking AND throttle spike
#define BRAKING_ARC_ANGLE 30.0f

// Take max(|Throttle| + 1, 1 - |Throttle|), this is how far to push dips and spikes towards that
// Goes from 0 to 1
// Throttle will be able to reverse by default
#define AGGRESSION 1.0f

// Defines whether or not to reverse throttle on braking
#define REVERSE_THROTTLE true

// Take [1000, 2000] and remap to [-1, 1] for both sticks and both axes
// This defines the dead zone applied to the output of the remapping
#define TRANSLATION_DEAD_ZONE 0.1f

// Rotational throttle has similar modulation, so we define the same dead zone
#define ROTATION_DEAD_ZONE 0.1f

/* Main Functions */
// Setup function
bool setupMotorsPWM() {
  // Setup constants
  MAX_THROTTLE_DEVIATION = (int)(((float) HIGH_SIGNAL - (float) LOW_SIGNAL) / 2.0f);

  // Bidirectional setup, just input neutral
  esc1.attach(ESC_1, LOW_SIGNAL, HIGH_SIGNAL);
  delay(2000); 
  esc2.attach(ESC_2, LOW_SIGNAL, HIGH_SIGNAL);
  delay(2000);
  esc1.writeMicroseconds(NEUTRAL);
  delay(2000);
  esc2.writeMicroseconds(NEUTRAL);

  // No checksums yet :(
  return true;
}


DShotRMT motor1(ESC_1, DSHOT600, false);
DShotRMT motor2(ESC_2, DSHOT600, false);
bool setupMotorsDshot() {
  MAX_THROTTLE_DEVIATION = (int)(((float) HIGH_SIGNAL - (float) LOW_SIGNAL) / 2.0f);
  motor1.begin();
  delay(20);

  motor2.begin(); 
  delay(20);

  // Enable 3D mode and save it — only needs to be done once ever
  for (int i = 0; i < 100; i++) {
    motor1.sendCommand(DSHOT_CMD_3D_MODE_ON);   // command 10
  }
  for (int i = 0; i < 100; i++) {
    motor1.sendCommand(DSHOT_CMD_SAVE_SETTINGS); // command 12
  }

  // Enable 3D mode and save it — only needs to be done once ever
  for (int i = 0; i < 100; i++) {
    motor2.sendCommand(DSHOT_CMD_3D_MODE_ON); 
  }
  for (int i = 0; i < 100; i++) {
    motor2.sendCommand(DSHOT_CMD_SAVE_SETTINGS);
  }

  // Re-arm after config change
  // unsigned long start = millis();
  // while (millis() - start < 5000) {
  //   motor1.sendThrottle(0);
  //   motor2.sendThrottle(0);
  // }

  delay(500);
  
  // Hold 1048 to ensure ESC is happy
  // start = millis();
  // while (millis() - start < 6000) {
  //   motor1.sendThrottle(1048);
  //   motor2.sendThrottle(1048);
  // }

  return true; 
}

int PWMtodShot(int pwm) {
  if (pwm == 1500) {
    return 1049; 
  }

  // 48 - 1047: full rev to min
  // 1049 - 2047: min to full for 

  //inputs:
  // 1000 - 1500 maps to 48 - 1047
  // 1500 - 2000 maps to 1049 - 2047

  // y = c + \frac{d - c}{b - a} \times (x - a) $$ 
  else if (pwm < 1500) { //back 
    return (int)(std::round(49.0 + (1500.0 - pwm) / (500.0) * (1047.0 - 49.0)));
  }
  else { //for
    return (int)(std::round(1049.0 + (pwm - 1500.0) / (500.0) * (2047.0 - 1049.0)));
  }
}

// Loop function to set motor throttles
// All inputs from [-1, 1]
// Heading_cosine denotes the dot product between heading and throttle vectors
bool stopLogic(float throttle_spinup, float throttle_x, float throttle_y, float heading_cosine) {
  // Get translational throttle magnitude D, not square rooted!
  D = min(1.0f, throttle_x*throttle_x + throttle_y*throttle_y);
  if (D < TRANSLATION_DEAD_ZONE) {
    D = 0.0f;
  }

  // Calculate the modulation function (determines where braking and spikes are)
  if (heading_cosine > HEADING_THRESHOLD) {
    M = 1.0f;
  } else if (-heading_cosine > HEADING_THRESHOLD) {
    M = -1.0f;
  } else {
    M = 0.0f;
  }

  // Calculate both motor throttle deviations (still outputs in range [-1, 1])
  if (REVERSE_THROTTLE) {
    Amplitude_Modulation = AGGRESSION * (abs(throttle_spinup) + 1.0f);
  } else {
    Amplitude_Modulation = -AGGRESSION;
  } 
  Modulation = M * D * throttle_spinup * Amplitude_Modulation;

  // Add to spinup throttle T and apply limits
  Motor_1_Throttle = throttle_spinup;
  Motor_2_Throttle = throttle_spinup;
  if (throttle_spinup < -0.1f || throttle_spinup > 0.1f) {
    Motor_1_Throttle += Modulation;
    Motor_2_Throttle -= Modulation;
  }
  Motor_1_Throttle = max(-1.0f, min(Motor_1_Throttle, 1.0f));
  Motor_2_Throttle = max(-1.0f, min(Motor_2_Throttle, 1.0f));

  int Motor_1_PWM_Val = (int)(Motor_1_Throttle * MAX_THROTTLE_DEVIATION + NEUTRAL); 
  int Motor_2_PWM_Val = (int)(Motor_2_Throttle * MAX_THROTTLE_DEVIATION + NEUTRAL); 

  // Rescale by multiplying by 500 and adding 1500
  // Set motor throttles
  #ifdef MOTORS
    // PWM WRITE
      // esc1.writeMicroseconds(Motor_1_PWM_Val);
      // esc2.writeMicroseconds(Motor_2_PWM_Val);

    // DSHOT WRITE
    motor1.sendThrottle(PWMtodShot(Motor_1_PWM_Val)); 
    motor2.sendThrottle(PWMtodShot(Motor_2_PWM_Val)); 


  #endif

  // Output telemetry
  #ifdef DISPLAY_SERIAL
    // Serial.println(HEADING_THRESHOLD);

    // Serial.print(heading_cosine);
    // Serial.print(", ");
    // Serial.print(M);
    // Serial.print(", ");
    // Serial.println(Modulation);

    // Serial.print(Motor_1_Throttle);
    // Serial.print(", ");
    // Serial.print(Motor_2_Throttle);
    // Serial.print(", ");
    // Serial.println(0);

    Serial.print(PWMtodShot(Motor_1_PWM_Val));
    Serial.print(", ");
    Serial.print(PWMtodShot(Motor_2_PWM_Val));
    Serial.print(", ");
    Serial.println(0);
  #endif

  // Again no checksums :(
  return true;
}

// Failsafe function
void killMotorsPWM() {
  esc1.writeMicroseconds(NEUTRAL);
  esc2.writeMicroseconds(NEUTRAL);
}

void killMotorsDshot() {
  motor1.sendThrottle(1048); 
  motor2.sendThrottle(1048); 
}

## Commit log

2026-06-02 init: initial version, added v0 firmware alongside docs and cad files
2026-06-02 v0 should actually be good now
    [Basic Teeth.step, Elec Housings.step, Main CAD.step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]
2026-06-03 Added Latest PCB files (V0 was pretty bad lol, maybe not the best idea to include that)
    [Eyeliner-PCB-V2-3V3_Cu.gbr, Eyeliner-PCB-V2-5V_Cu.gbr, Eyeliner-PCB-V2-B_Mask.gbr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]
